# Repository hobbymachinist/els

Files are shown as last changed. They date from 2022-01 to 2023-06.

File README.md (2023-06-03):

# STM32 - Electronic Leadscrew

Electronic Leadscrew with STM32

## Demos

Some short demos available on YouTube

https://www.youtube.com/channel/UCVE05OvPm0yVd1yQSVZ0YSA/videos

## Building

```
git clone https://github.com/libopencm3/libopencm3
export OPENCM3_DIR=$PWD/libopencm3

cd libopencm3
make

cd ../
git clone <repo-url>
cd els

# edit Makefile to pick target and a TFT version
make TFT=ILI9481

# or
make TFT=ILI9486

# or
make TFT=ILI9488
```

Some ILITEK ICs use a non-standard 556 16-bit colorspace, use `COLORS=TFT_RGB_556` option in that case.

```
make TFT=ILI9488 COLORS=TFT_RGB_556
```

## Technical documentation

See [Technical Documentation](docs/els.md)

## Design ideas & Reference

- https://github.com/clough42/electronic-leadscrew
- https://github.com/prototypicall/Didge

## Goals / Features

1. The initial software is going to focus on being functional.
2. There is huge scope for optimisation, which can be something I might look into down the track.
3. Eventually, I'd like to add a G-code parser and motion controller to enable optional CNC control.

### Working with limited testing

* Z axis control for manual turning and threading operations
* Soft limits on Z & X
* Hard limits on Z & X
* Backlash compensation for leadscrews
* Semi automated cycles:
    - Turning
    - Threading
    - External Tapers
    - Internal Tapers
    - External Arcs
* Optional DRO support for:
    - TTL optical scales

### Wishlist / TO DO

* Semi automated cycles:
    - Internal Arc
    - External groove
    - Internal groove
* Tool radius compensation

## Pull Requests

Please reach out to discuss any major rewrites or changes if you wish to merge the changes upstream.

A lot of the firmware was developed over a few years on and off when I could find time to code and think about how I'd use it.
I don't want to disappoint or stop anyone from improving the software or hardware design but the primary focus of this work is
for my own personal use and don't want anything to distract me from that in a significant fashion. I don't have plenty of spare
time to review design changes or major software changes.

## IMPORTANT - PLEASE READ

Lathes are not toys, you can get injured or hurt someone else if you're not careful. Use this software at your
own risk.

This software is not provided with any warranty or support. It has only had limited testing in a home / hobby use setting
and may result in you getting injured or your equipment getting damaged due to errors in programming.

The author does not take any responsibility for the use of this software by others and cannot be held liable for any damages
that may result from its use.

## LICENSE

https://opensource.org/licenses/GPL-3.0

Free to be used in any fashion without royalty but any changes to hardware or software should be attributed and publicly shared
for the benefit of others.

Some of the code in this project uses snippets of code from [Adafruit GFX](https://github.com/adafruit/Adafruit-GFX-Library/)

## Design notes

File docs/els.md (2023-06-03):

# ELSv2

[TOC]

## Demos

Some short demos available on YouTube

https://www.youtube.com/channel/UCVE05OvPm0yVd1yQSVZ0YSA/videos

## Hardware

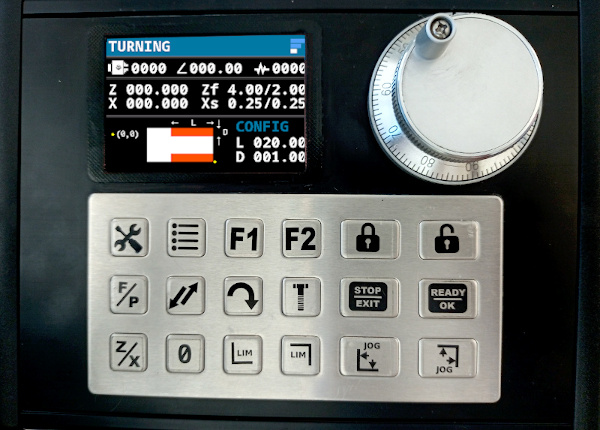
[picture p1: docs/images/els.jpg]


**IMPORTANT NOTE**

1. Ensure all signal cables are shielded.
2. Ensure the shielding is connected to ground at one end, close to the enclosure.
3. Ensure the enclosure is connected to power ground.
4. Always jog both axes to origin position (0, 0) before starting turning operations
    - This ensures any leadscrew backlash is taken care of in the lathe.
    - Allows the backlash compensation to kick in, ready for the turning steps.

### Kicad assets

All hw designs are done in Kicad 6.0.

- hw/els: The main board.
- hw/lcd: The LCD adapter for ILI9481 module

Optional extras:

- hw/buffer: Buffer and pulse shaper, helps keep the PUL signals going to the stepper drivers clean.
- hw/demo-driver: A standalone demo board with drv8825 for testing
- hw/power-clamp: Voltage clamp / suppression board.

### Main Board

Kicad files in hw/els

#### Active components

* Nucleo-F446RE https://www.st.com/en/evaluation-tools/nucleo-f446re.html
* GL850G USB HUB Controller
* CH340C USB UART
* FT24C64A EEPROM

#### Solder Bridge Changes and Modifications Needed to Nucleo64 446RE

The Nucleo 64 is connected to the main board USB hub with a small cable. Nucleo 446RE will need a fair few
jumper changes and soldering to permit the firmware to use the required GPIO pins.

Refer to the GPIO pins listed below in the GPIO Map, the solder bridges for these pins should be setup correctly. See Nucleo 446RE
documentation UM1724, Section 6.9 on Solder Bridges for more details. A quick summary for jumper settings and changes I've made.

| Jumper / Pad | State | Function |
|---|---|---|
| SB13 | REMOVE | PA2 for LCD |
| SB14 | REMOVE | PA3 for LCD |
| SB16 | REMOVE | HSE |
| SB21 | REMOVE | PA5 for LCD |
| SB50 | REMOVE | HSE |
| SB54 | REMOVE | HSE |
| SB55 | REMOVE | HSE |
| SB62 | ADD | Connects PA2 to D1 on CN9 |
| SB63 | ADD | Connects PA3 to D0 on CN9 |
| R35 | ADD | HSE, 0R or solder bridge |
| R37 | ADD | HSE, 0R or solder bridge |
| C33 | ADD | HSE, 18-22pF X7R Capacitor  |
| C34 | ADD | HSE, 18-22pF X7R Capacitor  |
| X3 | ADD | HSE, 8MHz HSE Crystal |
| D2 (CN9) | WIRE | Wire To CN3 TX for USART2 |
| D8 (CN5) | WIRE | Wire to CN3 RX for USART2 |

#### Using main board without USB hub & USB UART

The main board is primarily a breakout board for the Nucleo F446RE with a USB hub, USB USART controller
and additional terminal connectors. You can skip these (GL850G, CH340C and associated passives) and directly
wire PA9 and PA10 to the CN3 connectors marked RX and TX respectively. This will allow you to read the serial
comms via the onboard stlink CDC device.

The default UART baud rate in firmware is 921600, with 8 bits, no partity & 1 stop bit.

#### External Oscillator (HSE) on Nucleo 64

By default the firmware configures the clock to use the HSE. Nucleo 64 boards do not come with the crystal and passives
populated. Refer to UM1724 Section 6.7.1 for instructions on using HSE.

The following configuration is needed:
  - SB54 and SB55 OFF
  - R35 and R37 soldered
  - C33 and C34 soldered with 20 pF capacitors
  - SB16 and SB50 OFF

It's recommended to use an external crystal for better timing accuracy, but this is optional. If you want to use the
internal oscillator, set the `ELS_USE_HSE` directive to 0 in src/clock.c

#### EEPROM

This is again optional but without an external FT24C64A EEPROM, you will not be able to save the settings and the
defaults from constants.h will be used.

### TFT Breakout

Supported TFT 480x320 Displays

* ILI9481
* ILI9486
* ILI9488

AliExpress Links

* ILI9481 TFT LCD, https://www.aliexpress.com/item/1005001288341298.html
* ILI9486, ILI9488 TFT, https://www.aliexpress.com/item/1005001288341298.html

Kicad files in hw/lcd

This primarily a carrier / breakout board with an IDC ribbon cable connector to main board. The main board is
connected to the LCD module using an adapter board that breaks out the pins to a 16 pin IDC socket.

### Output buffer / pulse shaper

Kicad files in hw/buffer

Optional add-on for cleaning up the high frequency pulses from the main board to the stepper drivers. This needs to be powered
separately and co-located with the stepper drivers. You may not need this depending on the length of the signal cables from
the main board to the stepper drivers.

* CD4050BE, non-inverting hex buffer.
* CRE1S0505SC, isolated dc-dc converter 5v.

### Keypad

I used this because I had an unused one left over from a different project that did not work out. They're not cheap but they're
very reliable and resistant to liquids in the workshop. The seller can also laser etch the art for keypads if you're interested.

- IP65 18 Key, PS2 Keypad, https://www.aliexpress.com/item/1005002340320709.html

#### Input without keypad

You can make do with this for trying out the firmware by using UART as an input. To do it, edit src/usart.c and set
`ELS_USART_ENABLE_KEYPAD_INPUT` to 1

### Encoder

**IMPORTANT NOTE**

The spindle encoder PPR, along with the gear ratio and pulses per MM for Z axis determines the maximum spindle RPM and
thread pitch you can turn in threading operations. There is currently no warning displayed if the spindle PPR is less
than the minimum required PPR.

* Spindle Encoder: Optical 600PPR, https://www.aliexpress.com/item/4000392086291.html
* Hand wheel Encoder / pulser 100PPR 5v 4pin, https://www.aliexpress.com/item/32949618549.html

### Stepper motor & controller

* Z Stepper: 24HS40-5004D-E1000
  - https://www.omc-stepperonline.com/nema-24-closed-loop-stepper-motor-4-0-nm-566-56oz-in-encoder-1000cpr.html

* Z Controller: CL57Y
  - https://www.omc-stepperonline.com/y-series-closed-loop-stepper-driver-0-7-0a-24-50vdc-for-nema-17-23-24-stepper-motor.html

* X Stepper: NEMA23 1.2Nm 3A
  - https://www.aliexpress.com/item/1005002871654388.html

* X Controller: DM556
  - https://www.aliexpress.com/item/1005002628784693.html

### DRO

Supports TTL optical DROs and defaults to the commonly available 5uM resolution versions.

Most TTL optical DROs you get from China operate on a 5V logic level. You need to to get a DB9 panel or PCB socket (male)
and break out the 4 wires based on the wiring diagram for your DRO scale.

- +5V
- Ground
- Signal A
- Signal B

## Wiring / GPIO Map

```
PA0  - TFT Data
PA1  - TFT Data
PA2  - TFT Data
PA3  - TFT Data
PA4  - TFT Data
PA5  - TFT Data
PA6  - TFT Data
PA7  - TFT Data
PA8  - UNUSED
PA9  - USART TX
PA10 - USART RX
PA11 - DRO X-A (INTERRUPT)
PA12 - DRO X-B (INTERRUPT)
PA13 - UNUSED
PA14 - UNUSED
PA15 - UNUSED

PB0  - TFT RD
PB1  - DRO Z-A (INTERRUPT)
PB2  - UNUSED
PB3  - Spindle Enc A (INTERRUPT)
PB4  - Spindle Enc B
PB5  - DRO Z-B (INTERRUPT)
PB6  - TFT WR
PB7  - TFT RS
PB8  - TFT CS
PB9  - TFT RST
PB10 - EEPROM SCL
PB11 - N/A
PB12 - UNUSED
PB13 - Z ENA
PB14 - Z DIR
PB15 - Z PUL

PC0  - UNUSED
PC1  - UNUSED
PC2  - Input Enc A (INTERRUPT)
PC3  - Input Enc B
PC4  - PS/2 Keypad CLK (INTERRUPT)
PC5  - PS/2 Keypad DAT
PC6  - Spindle Enc A (Timer in Encoder mode)
PC7  - Spindle Enc B (Timer in Encoder mode)
PC8  - UNUSED
PC9  - UNUSED
PC10 - UNUSED
PC11 - UNUSED
PC12 - EEPROM SDA
PC13 - X ENA
PC14 - X DIR
PC15 - X PUL

PH0  - UNUSED
PH1  - UNUSED
```

## Keypad Layout

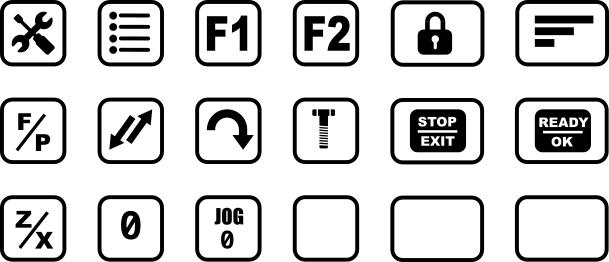
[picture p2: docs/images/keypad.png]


Keymap, left to right.

### Row 1

1. Settings
2. Lathe Functions
3. Special Function Key - F1
4. Special Function Key - F2
5. Keypad Lock / Unlock
6. Encoder multiplier change. Cyles through 1, 10 & 100.

### Row 2

1. Feed / Pitch
2. Reverse feed direction (not available in all functions)
3. Turning
4. Threading External
5. Stop Operation / Exit setting
6. Ready to start / Accept setting

### Row 3
1. Z/X axis setting
2. Zero Z / X axis
3. Jog to origin (depending on choice of Z or X axis setup)
4. Unused
5. Unused
6. Unused

## Lathe Functions

The manual turning and threading functions do not control the X axis / cross slide but allows turning
and threading operations at a given feed / pitch to a given length.

The remaining functions are stepper / servo driven on both Z (longitudinal along bed) and X (cross slide) axis.

All function screens display the spindle status at the top

1. Clockwise / Counter clockwise direction of spindle and RPM. Chuck icon is shown when RPM = 0
2. Angular position of the spindle in degrees. This can be used for any indexing functions.
3. Pulse counter, this is a function of the encoder PPR and wraps around. Threading operations synchronise to this value.

**NOTE**
1. Some lathe functions display diagrams where the stock to be removed is displayed in orange.
2. The origin (0,0) required for turning operations is displayed using a yellow dot.

### Settings

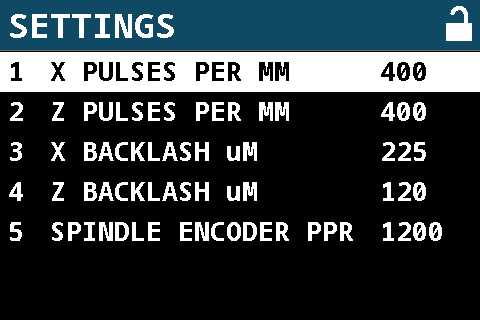
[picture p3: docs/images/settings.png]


#### X pulses per MM

X axis stepper / servo pulses per MM. This should include any gear ratios in transmission.

#### Z pulses per MM

Z axis stepper / servo pulses per MM. This should include any gear ratios in tranmission, especially if you're using
the gearbox.

#### X backlash uM

X backlash in microns. You can measure this by using a dial gauge against the cross slide and driving the stepper in
one direction for a full rotation and reversing to measure the amount of distance the stepper has to drive the axis before the
dial gauge indicates movement.

#### Z backlash uM

Z backlash in microns. Measure as above.

#### Spindle encoder PPR

Pulses per one revolution of the spindle. Note, this is usually the actual pulses generated by the encoder times any
gear ratios in drive mechanism. You can drive the encoder at 1.5-2x the speed of the spindle but pay attention to the
maximum RPM rating for the encoder.

#### X retract jog speed mm/s

Speed at which X axis retraction is done, can be slowed or sped up depending on gear / pulley ratios.

#### Z retract jog speed mm/s

Speed at which Z axis retraction is done, can be slowed or sped up depending on gear / pulley ratios.

#### X closed loop

If DRO is connected, then uses a simple closed loop traversal for linear movements on X axis. This can be particularly useful for turning stock to a specific diameter but it will depend on the accuracy of your DRO.

#### Z closed loop

If DRO is connected, then uses a simple closed loop traversal for linear movements on Z axis.

#### X DRO Invert

Invert direction for DRO on X Axis

#### Z DRO Invert

Invert direction for DRO on Z Axis

#### X DIR Invert

Invert stepper direction on X Axis

#### Z DIR Invert

Invert stepper direction on Z Axis

### Manual Turning

**NOTE**

When soft limits are turned on, with conventional turning the tool is moved from right to left along the Z axis at the
set feed rate until the minimum position is reached.

Steps:

1. Move tool to Z/X origin as required
2. Zero out Z and X axis optionally for DRO.
3. Set feed
4. Set length and enable soft limit (optional)
5. Turn on spindle
6. Press Ready to start
7. If soft limit is enabled, when the tool reaches the soft limit the feed will stop.
8. Back off tool, jog to Z origin.
9. Feed in tool and press Ready again

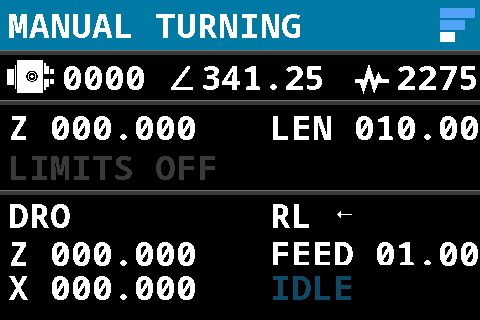
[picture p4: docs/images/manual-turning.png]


#### F/P

Set feed. The feed rate is independent of the spindle RPM at mm/s.

#### Reverse direction

Reverses feed direction. The usual direction is right to left towards spindle.

#### Z/X

1. Set Z axis, jogging
2. Pressing the button again switches to X axis setting, only used for zeroing the DRO reading (if available).

#### 0

Zero Z axis or X axis (DRO)

#### F1

Set the length to turn, Z soft limit target.

#### F2

Turns on / off soft limits. This will stop Z drive when the position reaches Z min.

#### Jog to Z origin

Jog Z axis to origin position

### Manual Threading

**NOTE**

When soft limits are turned on, with conventional turning the tool is moved from right to left along the Z axis at the
set pitch ratio until the minimum position is reached.

Steps:

1. Move tool to Z/X origin as required
2. Zero out Z and X axis
3. Set pitch
4. Set length
5. Turn on spindle
6. Press Ready to start
7. When the tool reaches the soft limit, it will stop.
8. Back off tool, press Jog to origin
9. Feed in tool and press Ready again

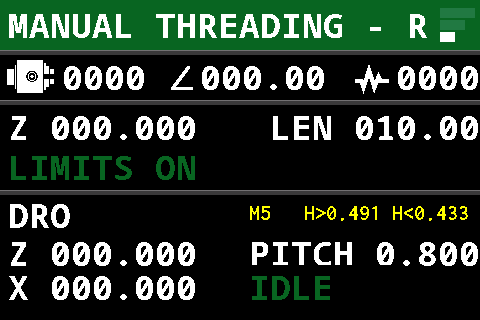
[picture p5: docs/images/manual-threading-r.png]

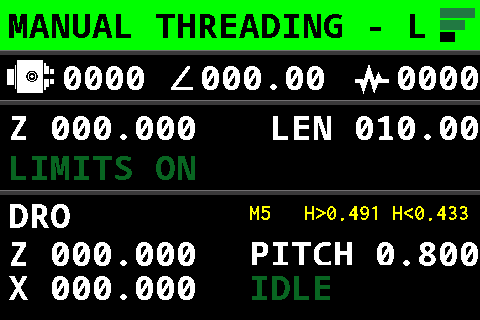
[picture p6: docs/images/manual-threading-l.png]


#### F/P

Choose pitch - the pitch determines the feed rate and this is tied to the rotation of the spindle.

You can pick a standard metric pitch with the displayed thread crest dimension. Pressing the key again will allow you to set
an arbitrary pitch value. This can be used to turn approximate imperial threads.

#### Reverse direction

While in pitch settings, pressing reverse feed direction allows you cut left hand threads or right hand threads.

#### Z/X

1. Set Z axis, jogging and setting min / max positions for virtual stop.
2. Pressing the button again switches to X axis setting, only used for zeroing the DRO reading.

#### 0

Zero Z axis or X axis (DRO)

#### F1

Set length

#### F2

Unused

#### Jog Z to Origin

Jog Z axis to 0 position

### Turning

Steps:

1. Move tool to Z/X origin as required
2. Zero out Z and X axis
3. Set roughing feed and feed for finish pass
4. Set the roughing depth of cut and depth of cut for finish pass
4. Set length and turning depth
5. Turn on spindle
6. Press Ready to start

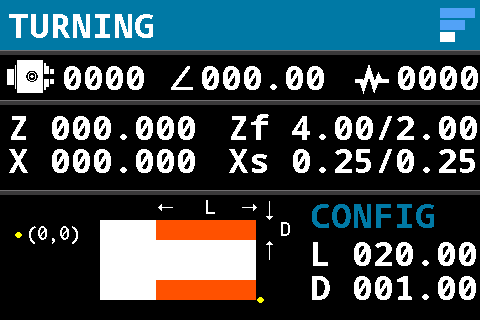
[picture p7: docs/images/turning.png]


#### F/P

Set feed & depth of cut.

NOTE: The feed rate is independent of the spindle RPM at mm/s.

Press key to cycle through

1. roughing feed rate in mm/s
2. finishing pass feed rate in mm/s
3. roughing depth of cut in mm
4. finishing pass feed rate in mm/s

#### Z/X

1. Z axis jogging.
2. Press key again for X axis jogging

#### 0

Zero Z axis or X axis (DRO)

#### F1

1. Set length
2. Press key again to set depth

#### F2

Display DRO or diagram.

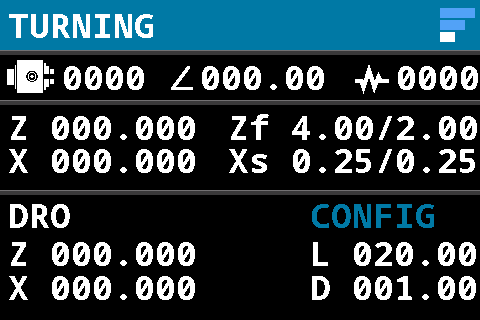
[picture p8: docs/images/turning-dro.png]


### Facing

Steps:

1. Move tool to Z/X origin as required
2. Zero out Z and X axis
3. Set feed
4. Set depth of cut on Z for each pass
4. Set length on Z axis to face and depth (radius of stock to face)
5. Turn on spindle
6. Press Ready to start

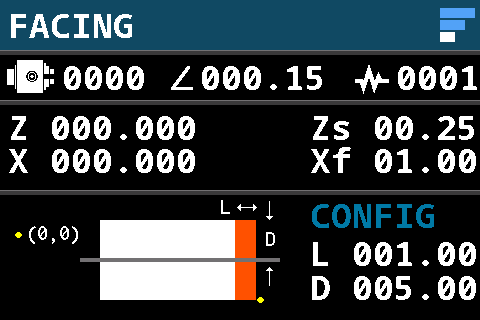
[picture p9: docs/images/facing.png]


#### F/P

Set feed (Xf) & depth of cut (Zs).

#### Z/X

1. Z axis jogging.
2. Press key again for X axis jogging

#### 0

Zero Z axis or X axis (DRO)

#### F1

1. Set length
2. Press key again to set depth

#### F2

Display DRO or diagram.

### Parting

Steps:

1. Move tool to Z/X origin as required
2. Zero out Z and X axis
3. Set feed (Xf)
4. Set depth of cut (radius of stock to part off)
5. Set retraction rate (Rx) if needed. e.g. if set to 2mm, this retracts the tool 5mm for every 2mm of in-feed.
5. Turn on spindle
6. Press Ready to start

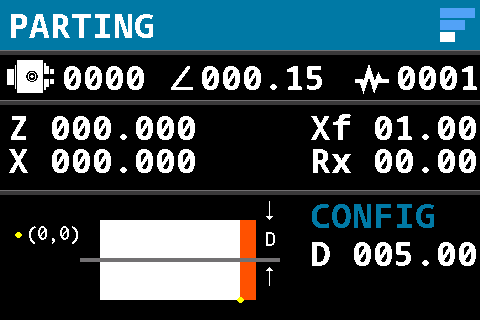
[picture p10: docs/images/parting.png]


#### F/P

Set feed (Xf) & retraction (Rx).

#### Z/X

1. Z axis jogging.
2. Press key again for X axis jogging

#### 0

Zero Z axis or X axis (DRO)

#### F1

Set total depth to part off, this is half the stock diameter ideally.

#### F2

Display DRO or diagram.

### Boring Pocket

Steps:

1. Move tool to Z/X origin as required
2. Zero out Z and X axis
3. Set feed and depth of cut
4. Set depth and turning radius
5. Turn on spindle
6. Press Ready to start

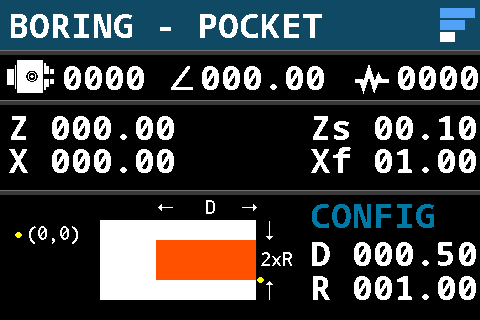
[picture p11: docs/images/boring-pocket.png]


#### F/P

1. Set feed. The feed rate is independent of the spindle RPM at mm/s.
2. Press key again to set depth of cut for turning pass.

#### Z/X

1. Z axis jogging.
2. Press key again for X axis jogging

#### 0

Zero Z axis or X axis (DRO)

#### F1

1. Set depth
2. Press key again to set radius

The diameter of the bore is twice the radius.

#### F2

Display DRO or diagram.

### Boring Hole

Steps:

1. Move tool to Z/X origin as required
2. Zero out Z and X axis
3. Set feed and depth of cut
4. Set depth and width for stock removal
5. Turn on spindle
6. Press Ready to start

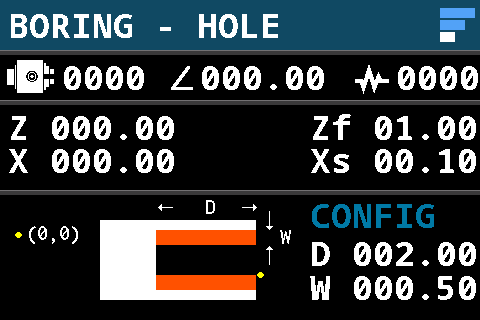
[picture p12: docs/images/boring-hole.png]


Use this if you have drilled a hole or performing boring operation with a through hole.

#### F/P

1. Set feed. The feed rate is independent of the spindle RPM at mm/s.
2. Press key again to set depth of cut for turning pass.

#### Z/X

1. Z axis jogging.
2. Press key again for X axis jogging

#### 0

Zero Z axis or X axis (DRO)

#### F1

1. Set depth
2. Press key again to set width of stock to remove.

#### F2

Display DRO or diagram.

### Knurling

Uses a form of bidirectional multi-start threading operation to cut knurls. Given the large pitch sizes required,
it's best to hand turn the spindle or use RPM < 30.

Steps:

1. Move tool to Z/X origin as required
2. Zero out Z and X axis
3. Set (L) length of the stock to knurl
4. Set (d) depth to cut
5. Set (D) diameter of stock
6. Set (A) lead angle, default to 30 deg.
7. Set (N) number of knurls.
8. Turn on spindle
9. Press Ready to start

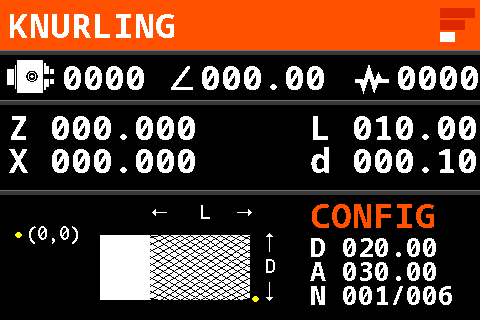
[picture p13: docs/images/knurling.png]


#### Z/X

1. Z axis jogging.
2. Press key again for X axis jogging

#### 0

Zero Z axis or X axis (DRO)

#### F1

Sets length, cut depth, diameter, lead angle and knurl count. Press F1 again to cycle through the settings.

#### F2

Display DRO or diagram.

### External Threading

Steps:

1. Move tool to Z/X origin as required
2. Zero out Z and X axis
3. Set pitch (and optionally thread height)
4. Set length and depth of cut
5. Turn on spindle
6. Press Ready to start

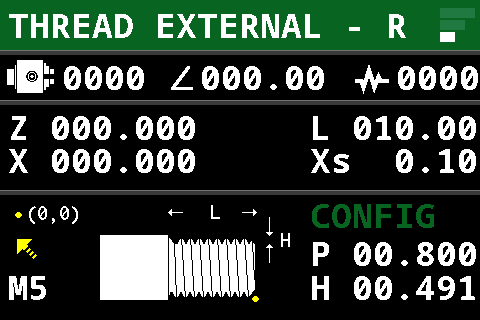
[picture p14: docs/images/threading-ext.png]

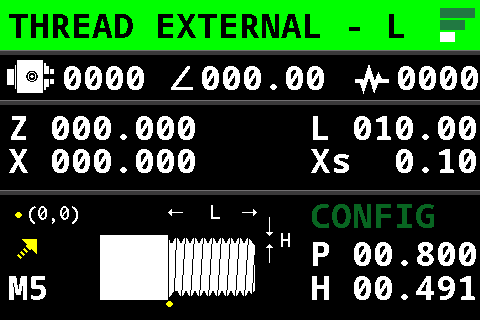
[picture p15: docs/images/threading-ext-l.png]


#### F/P

1. Select pitch, cycles through standard metric pitches.
2. Press key again to set an arbitrary pitch and thread height / depth.
3. Press "Reverse Direction (`</>`)" button to switch between RH and LH threads.

#### Z/X

1. Z axis jogging.
2. Press key again for X axis jogging

#### 0

Zero Z axis or X axis (DRO)

#### F1

IMPORTANT: The diagonal infeed hard codes the angle to 26.565° which is only valid for 60° thread profiles.

1. Set length of thread
2. Press key again to set depth of cut.
3. While in depth of cut selection press "Reverse Direction (`</>`)" button to switch between plunge and diagonal in-feed.

#### F2

Display DRO or diagram.

### Internal Threading

TODO: add support for LH threads and diagonal in-feed

Steps:

1. Move tool to Z/X origin as required
2. Zero out Z and X axis
3. Set pitch (and optionally thread depth)
4. Set length and depth of cut
5. Turn on spindle
6. Press Ready to start

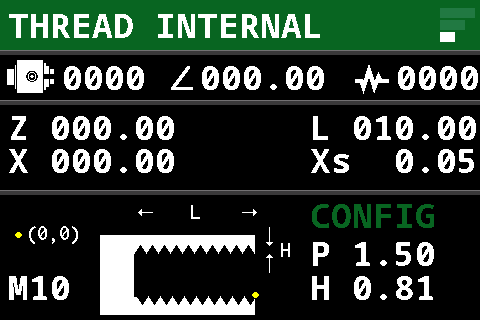
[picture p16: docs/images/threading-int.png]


#### F/P

1. Select pitch, cycles through standard metric pitches.
2. Press key again to set an arbitrary pitch and thread height / depth.

#### Z/X

1. Z axis jogging.
2. Press key again for X axis jogging

#### 0

Zero Z axis or X axis (DRO)

#### F1

1. Set length of thread
2. Press key again to set depth of cut.

#### F2

Display DRO or diagram.

### External Taper - Right

Steps:

1. Move tool to Z/X origin as required
2. Zero out Z and X axis
3. Set feed and depth of cut
4. Set length and depth of taper. Press F2 - The angle should be displayed in addition to DRO values.
5. Turn on spindle
6. Press Ready to start

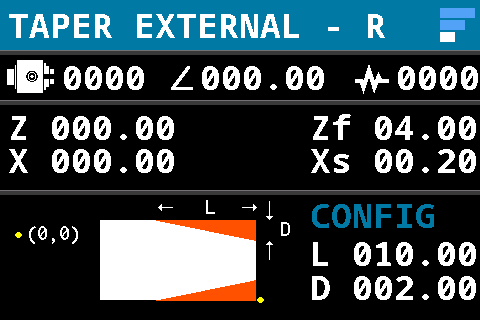
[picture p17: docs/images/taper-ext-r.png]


#### F/P

1. Select feed, mm/s.
2. Press key again to set depth of cut.

#### Z/X

1. Z axis jogging.
2. Press key again for X axis jogging

#### 0

Zero Z axis or X axis (DRO)

#### F1

1. Set length of taper
2. Press key again to set depth of taper.

#### F2

Display DRO or diagram. This also displays the taper angle.

### External Taper - Left

Steps:

1. Move tool to Z/X origin as required
2. Zero out Z and X axis
3. Set feed and depth of cut
4. Set length and depth of taper. Press F2 - The angle should be displayed in addition to DRO values.
5. Turn on spindle
6. Press Ready to start

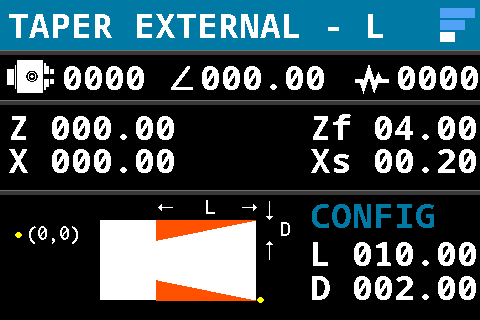
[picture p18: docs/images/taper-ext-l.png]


#### F/P

1. Select feed, mm/s.
2. Press key again to set depth of cut.

#### Z/X

1. Z axis jogging.
2. Press key again for X axis jogging

#### 0

Zero Z axis or X axis (DRO)

#### F1

1. Set length of taper
2. Press key again to set depth of taper.

#### F2

Display DRO or diagram. This also displays the taper angle.

### Internal Taper

Steps:

1. Move tool to Z/X origin as required
2. Zero out Z and X axis
3. Set feed and depth of cut
4. Set length and depth of taper. Press F2 - The angle should be displayed in addition to DRO values.
5. Turn on spindle
6. Press Ready to start

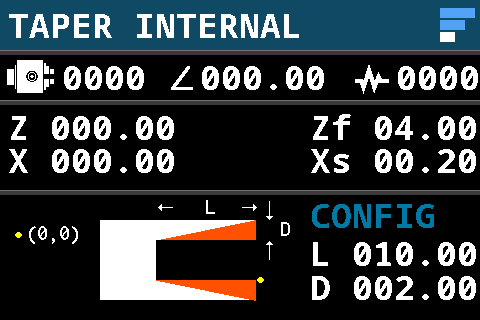
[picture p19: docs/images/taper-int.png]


#### F/P

1. Select feed, mm/s.
2. Press key again to set depth of cut.

#### Z/X

1. Z axis jogging.
2. Press key again for X axis jogging

#### 0

Zero Z axis or X axis (DRO)

#### F1

1. Set length of taper
2. Press key again to set depth of taper.

#### F2

Display DRO or diagram. This also displays the taper angle.

### Convex External - Right

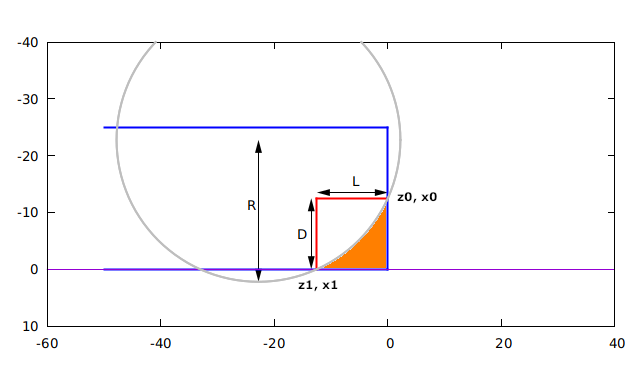
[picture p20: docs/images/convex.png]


Glossary:

1. (z0, x0) and (z1, x1), intersection of arc with stock.
2. Radius: Radius of the arc.
3. Depth: depth of arc, x1 - x0
4. Length: length of arc, z1 - z0

Varying the radius, length and depth will allow a variety of convex curves to be turned.

Steps:

1. Move tool to Z/X origin as required
2. Zero out Z and X axis
3. Set feed and depth of cut
4. Set radius, length and depth of arc.
5. Turn on spindle
6. Press Ready to start

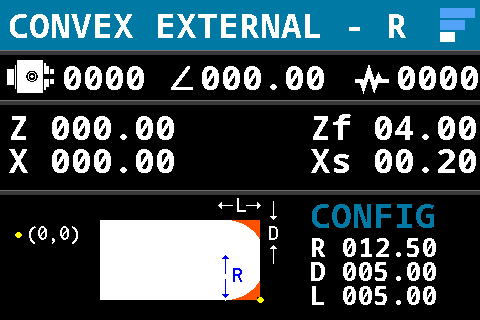
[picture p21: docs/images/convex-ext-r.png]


#### F/P

1. Select feed, mm/s.
2. Press key again to set depth of cut.

#### Z/X

1. Z axis jogging.
2. Press key again for X axis jogging

#### 0

Zero Z axis or X axis (DRO)

#### F1

1. Set radius of circle
2. Press key again to set depth.
3. Press key again to set length.

#### F2

Display DRO or diagram.

### Convex External - Left

Steps:

1. Move tool to Z/X origin as required
2. Zero out Z and X axis
3. Set feed and depth of cut
4. Set radius, length and depth of arc.
5. Turn on spindle
6. Press Ready to start

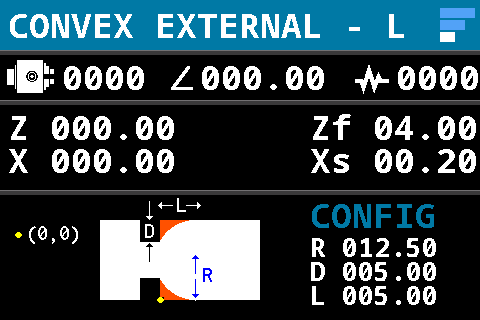
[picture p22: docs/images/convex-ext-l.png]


#### F/P

1. Select feed, mm/s.
2. Press key again to set depth of cut.

#### Z/X

1. Z axis jogging.
2. Press key again for X axis jogging

#### 0

Zero Z axis or X axis (DRO)

#### F1

1. Set radius of circle
2. Press key again to set depth.
3. Press key again to set length.

#### F2

Display DRO or diagram.

### Concave External - Right

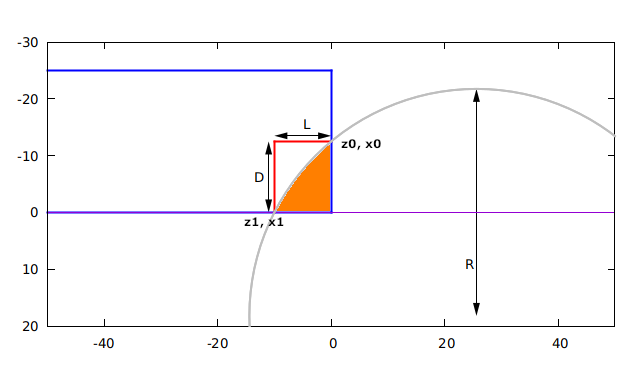
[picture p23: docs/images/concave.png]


Glossary:

1. (z0, x0) and (z1, x1), intersection of arc with stock.
2. Radius: Radius of the arc.
3. Depth: depth of arc, x1 - x0
4. Length: length of arc, z1 - z0

Steps:

1. Move tool to Z/X origin as required
2. Zero out Z and X axis
3. Set feed and depth of cut
4. Set radius, length and depth of arc.
5. Turn on spindle
6. Press Ready to start

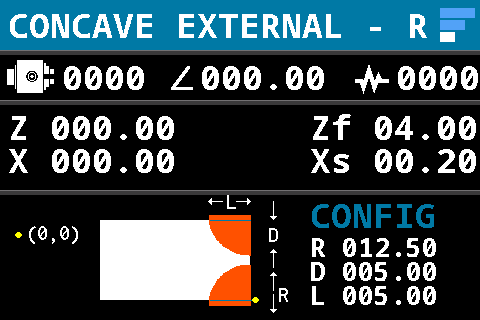
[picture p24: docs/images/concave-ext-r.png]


#### F/P

1. Select feed, mm/s.
2. Press key again to set depth of cut.

#### Z/X

1. Z axis jogging.
2. Press key again for X axis jogging

#### 0

Zero Z axis or X axis (DRO)

#### F1

1. Set radius of circle
2. Press key again to set depth.
3. Press key again to set length.

#### F2

Display DRO or diagram.

### Concave External - Left

TODO

### Rounded Groove

TODO

### Straight Groove

TODO

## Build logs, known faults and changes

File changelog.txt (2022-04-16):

2022-04-16

* increase stepper position resolution display
* add a new function for diamond cut knurling

2022-04-09

* replaced encoder acceleration with manual multiplier selection (1, 10, 100)
* added support for closed loop linear moves on Z & X axes
* updated convex turning to specify arbitrary convex arcs
* implementation for right handed concave arc
* reduced spindle encoder resolution for threading, improves responsiveness

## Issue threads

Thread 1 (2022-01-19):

G-code parser

ebo, 2022-01-19:
Decades ago I wrote a g-code parser using Spirit+ (part of the Boost libraries).  It came complete with runtime overloading of commands (so you could run different flavors of RD274*).  That project was WAY overkill and probably would not fit into what you have in mind, but I could probably salvage chunks to be useful.  So, tell me what you want the parser to do, and maybe PM me, and we can discuss seeing if any of it would be useful.

hobbymachinist, 2022-01-19:
Thanks @ebo, the rough plan is to get a modified version of Grbl integrated as a module to allow CNC control of X and Z axis along with spindle sync. If that works, I can get rid of the bespoke stepper controller in els and rewrite almost all the stock turning operations as canned cycles that can be fed into Grbl.

qtron, 2022-06-02:
Hi HM,
help! i'm stuck.. not familiar w github at all, lost a LOT of time trying to find the documentation, circuit diagram & gerber files etc.. i saw a gpio list but not sure what that all means!
i have built a Russian 2 axis arduino Mega ELS & seems to work, but i much prefer yours with the magic, albeit expensive!! keypad.
- I also can't find info on how U re labelled it, so nicely!!
- Do U have a list of the specs of the ELS (i dont mean characteristics)?
- Can U move the els in 0.01mm increments?
- What is the max allowable backlash your s/w can cope with?
- i saw the vid of the failed reverse taper.. what was wrong? some words would help!

Without a circuit diagram i have no way of knowing how to set it up, & install/ program the Eprom i saw mentioned.. where did U get it from? How did U program it?

I see its been a while since u were here last, so hope ur ok.

I did download the zip file for the code but cant see how to download the documentation.
i have no idea what a fork is, pull requests, etc.. does pull mean remove ur files?!!
Sorry but i find github strange indeed.
eg, Why does one need to see the inner workings of a gerber file here?
i have kicad & use JLCPCB quite a bit , could see gerber files but they are all individual - how do U download all at once? surely they are zipped?
Thanks!
Qtron

hobbymachinist, 2022-06-03:
The schematics are split into multiple modules, you can open them up in Kicad to have a look.

Main board: https://github.com/hobbymachinist/els/blob/main/hw/els/els.sch  or https://github.com/hobbymachinist/els/blob/main/hw/els/els.pdf
LCD breakout https://github.com/hobbymachinist/els/blob/main/hw/lcd/lcd.sch

> i saw a gpio list but not sure what that all means!

Here's a very brief summary how the pins are mapped,
https://github.com/hobbymachinist/els/blob/main/src/gpio.h#L25-L81

You are expected to have some knowledge of electronics, microcontrollers and writing firmware. This project is not designed to be consumer ready if you're not able to understand how all of these go together unfortunately.

> Do U have a list of the specs of the ELS

What do you mean by specs ?

> Can U move the els in 0.01mm increments?

This depends on your servo / stepper driver settings (usually called micro steps), the smallest increment I can move my axes is 0.0025mm

> What is the max allowable backlash your s/w can cope with?

Any arbitrary amount, but this needs to be constant and cannot vary by direction. I have since stopped relying on this as the backlash can drift over time leading to inaccurate movements.

I would recommend switching over to ball screw if you want 2 axes precision control or use an optical DRO scale and connect that to the ELS. The ELS now supports limited closed loop movement on both axis by using the DRO for feedback and compensates for backlash accordingly.

> i saw the vid of the failed reverse taper.. what was wrong? some words would help!

It was a control loop bug and was not setting the stepper direction pulse correctly, I've fixed it.

> does ur ELS do the calcs on the fly, like Clough42's ELS?

yes, the micro controller used is very capable. STM32F446RE can handle a lot more if the internal features are use correctly. I'm not taking advantage of all the features yet and it seems to work fine for me.

> Why does one need to see the inner workings of a gerber file here?
> i have kicad & use JLCPCB quite a bit , could see gerber files but they are all individual - how do U download all at once?

If you have Kicad, you can open the project files under the hw directory and have a look, export the gerbers as needed for your purpose but as I said, this project is not going to be ready to use out of the box unless you have some basic knowledge of microcontrollers, electronics and firmware programming.

hobbymachinist, 2022-06-03:
@qtron if you're not comfortable with a full DIY solution, I would recommend you take a look at Rocketronics ELS https://www.rocketronics.de/en/els/. It is ready to use and comes with excellent documentation.

qtron, 2022-06-03:
hiya HM,
i am comfortable! as i said i built the russian 2 axis els..(ver 7e2)
its not so easy to use.

i just need the info. of your nice creation to proceed, if possible.
Yours is the only one with knurling,
  (as well as ricketronics does have issues.
a guy on youtube evaluated it, and some glitches can be seen, like not starting threading! its expensive too ).

pls advise:
does yours do calcs on the fly?

how do i find the cct diagram to load into kicad?
As i said, navigating thru Github trying to find downloads is hard! (obviously not for some!)
PLEASE advise..
thankyou😃

On 3 June 2022 12:34:48 GMT+10:00, hobbymachinist ***@***.***> wrote:
***@***.*** if you're not comfortable with a full DIY solution, I would recommend you take a look at Rocketronics ELS https://www.rocketronics.de/en/els/. It is ready to use and comes with excellent documentation.
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
..
Sent from mob. Ph.

qtron, 2022-06-03:
sorry HM, i just found your previous email! much appreciated
the rocketronics unit basic ver 4, delivered is $422 AUD.

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
***@***.*** if you're not comfortable with a full DIY solution, I would recommend you take a look at Rocketronics ELS https://www.rocketronics.de/en/els/. It is ready to use and comes with excellent documentation.
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
..
Sent from mob. Ph.

qtron, 2022-06-03:
i am most grateful for the links to the files, but is there a place in github where i can download them, to get into kicad?

by move 0.01mm , i meant move from the control panel, not microstep movement..

Specs: like max settable X & Z motion,
respose time after go button pressed,
lag time of tool vs steps issued,
any step misses at high speed,

absolutely wonderful re closed loop.
i saw the glass scale on your Z motion, (but didnt know if it was just DRO).

BTW,
i saw in MEW that Joe Noci (of Nairobi) uses a rattle damper on his stepper to kill any resonance! it is supposed to help greatly , accel. from zero.

kind regards,

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
..
Sent from mob. Ph.

hobbymachinist, 2022-06-03:
Go to the repository page, https://github.com/hobbymachinist/els and download the zip file as shown

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

> by move 0.01mm , i meant move from the control panel, not microstep movement..

0.005mm

> Specs: like max settable X & Z motion,

There are no soft limits, only what you set the limits to in the program.

> respose time after go button pressed,

Probably 50-100ms. If you're thinking about threading it synchronises to the encoder counter so even if you press it will only start at the spindle position when encoder counter is at a certain value.

> lag time of tool vs steps issued,

speed of light :)   it's probably a few microseconds due to the stepper / servo drivers.

> any step misses at high speed,

not that I have noticed, I use closed loop hybrid steppers that will stall if they cannot keep up but there is no acceleration support for threading - so your mileage may vary depending on your hardware choice.

qtron, 2022-06-03:
thanks again😃
i had already downloaded the zipped MCU f/w.
i mean download the schematics, the wiring hookup diagram to the eprom, & the overall layout..

i saw the list from the links u sent earlier, clicked on ''copy path'', tried
''permlink copy'' etc. .. nothing happened.
just dunno how to get the sch into kicad,
and how to get the zipped gerber files.
cheers,

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
..
Sent from mob. Ph.

Closed 2022-06-03.

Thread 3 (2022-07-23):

Questions

kzali, 2022-07-23:
Hi
Firstly I'd like to thank you for such a well though project.  I am happy to say that I have gotten all the PCB's and the Neucleo board
The LCD, Encoder, Keyboard, and the hand wheel are on the way.  I intend to build it slowly as have beginner level skills (largely in simple Arduino projects.)

1.  I am having a hard time sourcing the FT24C64A EEPROM, CH340C USB UART and the GL850G USB HUB Controller, here in Australia.  I understand from your very detailed technical
    documentation that I can do without the CH340C and the GL850G (and their passive components)  I will however directly wire PA9 and PA10 to the CN3 connectors marked RXand TX on the Nucleo.

2.  There seem to be many i2c 8 pin 64k EEPROMS on au.rsonline and other suppliers! Any suggestions/alternate will be greatly appreciated.

3.  I am not clear what this means "Nucleo 446RE will need a fair few jumper changes and soldering to permit the firmware to use the required GPIO pins. Refer to the GPIO pins listed below, the solder bridges for these pins should be setup correctly. See Nucleo 446RE documentation UM1724, Section 6.9 on Solder Bridges."  I have tried to figure it out without any success from the UM1724 documentation.  I am assuming that the jumper changes are on the Neuclo but am confused about the 15 TerminalBlock_bornier-
2_P5.08mm and suspect that the bridges are related to this.  Your direction will be highly appreciated **(perhaps an image of the populated board.)

5.  After failing to setup the Toolchain on windows via cygwin, I succeeded in setting it up on a Raspberry Pi 400 and it compiled without any issues.  Was wondering if this can be accomplished with CubeMX!

6.  I intend to use the demo driver board to first test this with a toy lathe (Thefirsttool Tz20002mr) that I have had for a while, using Nema 17 motors.  And Eventually install on My Sieg C3.

I am located in the Sydney region and have extra PCB's will be happy to send you a couple of sets if you need it considering you are in Australia.  My email: kzaliaust@gmail.com.  Many thanks for your help

Regards
Kamran Zali

Closed 2022-07-23.

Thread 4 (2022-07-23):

Questions

kzali, 2022-07-23:
Hi
Firstly I'd like to thank you for such a well though project. I am happy to say that I have gotten all the PCB's and the Neucleo board
The LCD, Encoder, Keyboard, and the hand wheel are on the way. I intend to build it slowly as have beginner level skills (largely in simple Arduino projects.)

I am having a hard time sourcing the FT24C64A EEPROM, CH340C USB UART and the GL850G USB HUB Controller, here in Australia. I understand from your very detailed technical
documentation that I can do without the CH340C and the GL850G (and their passive components) I will however directly wire PA9 and PA10 to the CN3 connectors marked RXand TX on the Nucleo.

There seem to be many i2c 8 pin 64k EEPROMS on au.rsonline and other suppliers! Any suggestions/alternate will be greatly appreciated.

I am not clear what this means "Nucleo 446RE will need a fair few jumper changes and soldering to permit the firmware to use the required GPIO pins. Refer to the GPIO pins listed below, the solder bridges for these pins should be setup correctly. See Nucleo 446RE documentation UM1724, Section 6.9 on Solder Bridges." I have tried to figure it out without any success from the UM1724 documentation. I am assuming that the jumper changes are on the Neuclo but am confused about the 15 TerminalBlock_bornier-
2_P5.08mm and suspect that the bridges are related to this. Your direction will be highly appreciated **(perhaps an image of the populated board.)

After failing to setup the Toolchain on windows via cygwin, I succeeded in setting it up on a Raspberry Pi 400 and it compiled without any issues. Was wondering if this can be accomplished with CubeMX!

I intend to use the demo driver board to first test this with a toy lathe (Thefirsttool Tz20002mr) that I have had for a while, using Nema 17 motors. And Eventually install on My Sieg C3.

I am located in the Sydney region and have extra PCB's will be happy to send you a couple of sets if you need it considering you are in Australia. My email: [kzaliaust@gmail.com](mailto:kzaliaust@gmail.com). Many thanks for your help

Regards
Kamran Zali

hobbymachinist, 2022-07-23:
> I intend to build it slowly as have beginner level skills (largely in simple Arduino projects.)

Just ask questions on this issue, so it can function as a reference for others. Just setting the expectations and caveats perhaps too late sine you're committed now :)

- It's a personal project I work on in my spare time - so there's definitely a few rough edges.
- I would normally guide people towards Acorn, Masso, Mach4 or even LinuxCNC - I only started building this because I like using my lathe manually most of the time, ELS is something that helps with repetitive work / tapers etc.
- Backlash compensation is extremely tricky to get right, especially on Z with the way half nuts engage determining the backlash at times. So backlash can potentially vary over time in my observation, needs calibration every single time before you do something.
- I have installed an optical linear scale with 5uM resolution and use this for closed loop feedback instead of backlash compensation.

> I am having a hard time sourcing the FT24C64A EEPROM, CH340C USB UART and the GL850G USB HUB Controller, here in Australia.

I would skip the USART and USB HUB controller, it's only there because I was initially planning to use the HUB for a second daughter board in the future.

> I will however directly wire PA9 and PA10 to the CN3 connectors marked RXand TX on the Nucleo.

This will work fine, I use this for my second dev kit I use for testing.

> There seem to be many i2c 8 pin 64k EEPROMS on au.rsonline and other suppliers! Any suggestions/alternate will be greatly appreciated.

You should be able to use any 24C64A eeprom in the compatible SO-8 package. They all have the same pinouts and usually have the same read / write control loop / implementation.

>  I have tried to figure it out without any success from the UM1724 documentation. I am assuming that the jumper changes are on the Neuclo but am confused about the 15 TerminalBlock_bornier-2_P5.08mm and suspect that the bridges are related to this.

Can you elaborate ? for each of the GPIO listed in the UM1724 solder bridge section, you need to remove or add the jumper as explained in the user manual to allow the pin to be routed to the external GPIO (disconnected from the default Nucleo function).

Additionally you will also need to
- solder the bridges for the external high frequency (HSE) crystal.
- solder 2 capacitors, I think 18pF

> After failing to setup the Toolchain on windows via cygwin, I succeeded in setting it up on a Raspberry Pi 400 and it compiled without any issues. Was wondering if this can be accomplished with CubeMX!

I use libopencm3, so CubeMX will no help. If you're using Windows 10, you should have better luck with WSL and ARM GCC.

http://cs107e.github.io/guides/install/wsl/

> I intend to use the demo driver board to first test this with a toy lathe (Thefirsttool Tz20002mr) that I have had for a while, using Nema 17 motors. And Eventually install on My Sieg C3.

Yeah go for it, pay attention to polarity, DRV8825 is very picky, fries easy and needs a heat sink.

I have a fair few extra boards around, once the STM32 shortage eases I will most likely respin the board to ditch the Nucleo 64. The only reason I went with that is it was it was impossible to get STM32F446 on tape when I started building this :)

Good luck!

hobbymachinist, 2022-07-23:
and use shielded cables for everything, DC motors or VFD + AC 3ph motor, TFT etc everything is a noise generator, so shield everything :|

kzali, 2022-07-23:
Hi many thanks for a prompt response
> * Pay attention to cable shielding, if possible use ferrite ribbon cable for the TFT (TFTs are very noisy at high speed).
Noted had to do shielded cabling even for a Grbl controller

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

I had meant "There seem to be many i2c 8 pin 64k EEPROMS on au.rsonline and other suppliers!  But  NO 24C64A in SO-8 (seems to be a shortage of these)  So any suggestions?
>
> > I have tried to figure it out without any success from the UM1724 documentation. I am assuming that the jumper changes are on the Neuclo but am confused about the 15 TerminalBlock_bornier-2_P5.08mm and suspect that the bridges are related to this.
>
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
Thankyou

deepfryed, 2022-07-23:
> I had meant "There seem to be many i2c 8 pin 64k EEPROMS on au.rsonline and other suppliers! But NO 24C64A in SO-8 (seems to be a shortage of these) So any suggestions?

wow, even eeproms ?! geee

try LCSC https://lcsc.com/products/EEPROM_502.html?keyword=24C64A

> I am assuming that the jumper changes are on the Neuclo

Yes, all of the jumper changes are on the Nucleo 64 board. No need to to bodge anything on the ELS main board PCB, unless you need to customise something.

You will need to do some point to point wiring for DRO connection if you choose to add that.

hobbymachinist, 2022-07-23:
> I had meant "There seem to be many i2c 8 pin 64k EEPROMS on au.rsonline and other suppliers! But NO 24C64A in SO-8 (seems to be a shortage of these) So any suggestions?

wow, even eeproms ?! geee

try LCSC https://lcsc.com/products/EEPROM_502.html?keyword=24C64A

> I am assuming that the jumper changes are on the Neuclo

Yes, all of the jumper changes are on the Nucleo 64 board. No need to to bodge anything on the ELS main board PCB, unless you need to customise something.
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
hobbymachinist, 2022-08-01:
@kzali did you manage sourcing the EEPROM, this might be pin and protocol compatible but half the storage size which may be enough (you need to double check the datasheet) and is available from Rockby in Melbourne. The firmware code needs to be modified if you use this.

https://www.rockby.com.au/SearchresSql_12.cfm?Searchkey=AT24C32N

kzali, 2022-08-01:
> @kzali did you manage sourcing the EEPROM, this might be pin and protocol compatible but half the storage size which may be enough (you need to double check the datasheet) and is available from Rockby in Melbourne. The firmware code needs to be modified if you use this.
>
> https://www.rockby.com.au/SearchresSql_12.cfm?Searchkey=AT24C32N

@hobbymachinist Thanks for the heads up,  I will be visiting my country of origin and have a micro Shenzhen, in my home town and have sourced all the components there.  At better prices that Aliexpress as well!  In fact will be carrying one set of boards as its very cheap to have them populated by professional services.  Will probably bring some extra components, for future projects.  Have the keyboard with me and the encoder and the pulse wheel expected today.

Still was only able to setup the toolchain on the raspberry pi 400 while on WSL and a Ubuntu VM I get this error  (Don't know what I am doing wrong!
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
So googling away

hobbymachinist, 2022-08-01:
It might be easier to read if you copy paste the error text. The screenshot is hard to read on my phone.

I can see `-I/home/billa/els/libopencm3/include`  is there a libopencm3 directory there ?

> Will probably bring some extra components, for future projects.

excellent, see if you find a cut tape of stm32f446re at good price lol

kzali, 2022-08-01:
billa@billa:~/libopencm3$ cd ~
billa@billa:~$ cd els
billa@billa:~/els$ arm-none-eabi-gcc  --version
arm-none-eabi-gcc (15:9-2019-q4-0ubuntu1) 9.2.1 20191025 (release) [ARM/arm-9-branch revision 277599]
Copyright (C) 2019 Free Software Foundation, Inc.
This is free software; see the source for copying conditions.  There is NO
warranty; not even for MERCHANTABILITY or FITNESS FOR A PARTICULAR PURPOSE.

billa@billa:~/els$ make
rules.mk:60: Cannot find libopencm3 library in the standard search paths.
rules.mk:61: *** Please specify it through OPENCM3_DIR variable!.  Stop.
billa@billa:~/els$ export OPENCM3_DIR=$PWD/libopencm3
billa@billa:~/els$ make
Using /home/billa/els/libopencm3 path to library
arm-none-eabi-gcc -Os -std=c99 -ggdb3 -mthumb -mcpu=cortex-m4 -mfloat-abi=hard -mfpu=fpv4-sp-d16 -Wextra -Wshadow -Wimplicit-function-declaration -Wredundant-decls -Wmissing-prototypes -Wstrict-prototypes -fno-common -ffunction-sections -fdata-sections -DGIT_SHA=\"9fbd06c\" -DBUILD_TS=\"2022-08-02T09:30:14\" -Isrc -DVERBOSE=0 -std=gnu99 -mfloat-abi=hard -Wno-unused-parameter -Wno-unused-variable -Wno-unused-function -Os -DSTM32F446 -DSTM32F4xx -MD -Wall -Wundef -DSTM32F4 -I/home/billa/els/libopencm3/include  -o obj/src/convex_ext_l.o -c src/convex_ext_l.c
src/convex_ext_l.c:9:10: fatal error: libopencm3/cm3/dwt.h: No such file or directory
    9 | #include <libopencm3/cm3/dwt.h>
      |          ^~~~~~~~~~~~~~~~~~~~~~
compilation terminated.
make: *** [rules.mk:187: obj/src/convex_ext_l.o] Error 1
billa@billa:~/els$

hobbymachinist, 2022-08-02:
@kzali Is there a `/home/billa/els/libopencm3/include/libopencm3` folder ? I think that's what gcc is complaining about

kzali, 2022-08-02:
billa@billa:~$ cd libopencm3
billa@billa:~/libopencm3$ ls
COPYING.GPL3  COPYING.LGPL3  HACKING  HACKING_COMMON_DOC  Makefile  README.md  doc  els  include  ld  lib  locm3.sublime-project  mk  scripts  tests
billa@billa:~/libopencm3$ cd include
billa@billa:~/libopencm3/include$ ls
libopencm3  libopencmsis

yes the folders are there

hobbymachinist, 2022-08-02:
heh, `-I/home/billa/els/libopencm3/include` so that's wrong

it should be /home/billa/libopencm3, check your OPENCM3_DIR env variable

kzali, 2022-08-02:
Thanks will check that and give it a shot
Alas my terrible Linux skills.  Appreciate your help, I guess that's how
one learns!

On Tue, 2 Aug 2022, 10:50 am hobbymachinist, ***@***.***>
wrote:

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

kzali, 2022-08-02:
> heh, `-I/home/billa/els/libopencm3/include` so that's wrong
>
> it should be /home/billa/libopencm3, check your OPENCM3_DIR env variable

@hobbymachinist  Thanks cleaned the env variable's and export OPENCM3_DIR=$PWD/libopencm3
vola it worked like magic!!  Thanks to you learnt a lot today.
Cheers

Closed 2022-08-20.

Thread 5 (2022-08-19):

2 DRO and display issue

UberChmonya, 2022-08-19:
Hi, I really like your project! Is it possible to create an encoder for each axis (MPG) in the project? It would be very nice. I completely removed the mechanical control of the axes from the machine. Also, I could not find a display module for sale. What can replace it?

hobbymachinist, 2022-08-20:
Thanks.

Sorry, I don't plan on adding support for multiple MPG encoders - I need the extra pins for additional features I'm working on. You can customise the code to suit your needs though, but I most likely will not be able to add support for it.

>  I could not find a display module for sale. What can replace it?

Did you check AliExpress or eBay ? ILI9481 based 480x320 TFT modules are fairly common

e.g.
https://www.aliexpress.com/item/1984270730.html

AndreyFly007, 2022-09-05:
Good day friend.

> I need the extra pins for additional features I'm working on

Maybe there are details about which pins and interrupts will be occupied?

I started to repeat your device. I changed the printed circuit board, placed the connectors that are convenient for me. Aliexpress did not have the recommended screen. Therefore, the screen had to be ordered without an arduino shield. The screen will connect directly to the ELS, without a shield. Soon I will be able to share the printed circuit board (it remains to finish a few little things).
I would be very grateful if you could expand the list of which pins and interrupts will be used.

At the moment, to use the second MPG, I have used pins PC0, PC1, as well as an interrupt on PC0.
until the PCB is ordered, I have time to adjust the circuit for further compatibility with your project.

AndreyFly007, 2022-09-05:
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

hobbymachinist, 2022-09-05:
@AndreyFly007

I've left PC0, PC1, PC10, PC11, PH0, PH1 free for now. Rest are reserved, I might be able to free up some more pins after I change the board design to convert differential DRO signals to single ended.

The primary (MPG) encoder is used for menu selection and along with MPG for X and Z travel, I'd be interested to see how you're using 2 encoders in the user interface.

AndreyFly007, 2022-09-05:
> The primary (MPG) encoder is used for menu selection and along with MPG for X and Z travel, I'd be interested to see how you're using 2 encoders in the user interface.

the first MPG works without changes, menus, moving the Z axis. The second MPG will only be for the X axis.
My machine does not have mechanical manual movement handles. The Z and X axes can only be controlled electronically.

AndreyFly007, 2022-09-05:
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

hobbymachinist, 2022-09-05:
@AndreyFly007 I don't want to discourage you, but it looks like you've done extensive changes. I would pause and think about what you really want in the end. It sounds like conversational wizard with Linux CNC, Mach 4 or Acorn would be much better. You can do everything this project does and much more. You can also use 2 MPG wheels for dual axis control.

This project is quite experimental and I'm doing it for fun, you're more than welcome to do the same but in terms of investing time and money to get the features you're after the above mentioned options could be better.

hobbymachinist, 2022-09-05:
@AndreyFly007 See Kent's channel for how he's done it, https://www.youtube.com/watch?v=JdhNRhK3TCY. You can reach out to him to ask for tips if that's the route you want to take.

AndreyFly007, 2022-09-05:
I like your project. This project has great potential for development. Superficially looked through the code, found many interesting solutions for synchronizing the spindle with the feed. There is almost everything for working with Gcode, the only thing left is the parser procedure.
I know about all ready-made solutions (mach3, mach4, linux cnc), but they are not interesting to me. I love DIY projects. Your project is a great opportunity to plunge into the world of STM32.

hobbymachinist, 2022-09-05:
There's a lot of scope for improvement, especially with PWM and DMA but that will need remapping of GPIO pins. For what it's doing at the moment, it's good enough. I might revisit optimisations once I have all the basic features implemented.

AndreyFly007, 2022-09-07:
there is a very good example of Gcode parser on 2 axis on Github. For G0, G1, G2, G3 Gcode already has all the functions in your code. Code with a good description for Arduino, and can help you get started with GCode

[https://github.com/MarginallyClever/GcodeCNCDemo/tree/master/GcodeCNCDemo2Axis](url)

hobbymachinist, 2022-09-08:
@AndreyFly007 thanks, I'll take a look. There are couple of good options for GCode but I'm leaning towards a modified version of GRBL and a complete rewrite of the ELS functions to use the motion controller in GRBL. This would allow it to keep up with any newer versions of GRBL as a GCode processor, motion & stepper / servo controller allowing it to work with CAM post processors.

AndreyFly007, 2022-09-08:
I spent a lot of time looking for GRBL firmware for a lathe. None of them work with spindle synchronization. All I found is GRBL HAL, but even there it says that support for synchronization with the spindle is in test mode.
Прочитав много форумов, я пришел к выводу, что 90% операторов токарного станка пишут Gcode вручную в блокноте. для CNC токарного станка достаточно иметь G0, G1, G2, G3, G4, G32, G33, G76, G90, G91, G92. Для выполнения этих кодов в Вашей программе уже все есть. У Вас есть код для перемещения линейно и по радиусу, это G0, G1, G2, G3. Очень легко реализовать G4, это пауза. G32, G33, это нарезание резьбы. G76 это нарезание резьбы в цикле за несколько проходов. Остальные команды, это команды работы с системой координат.
Все CAM post processors настраиваются на Gcode поддерживаемый станком. 1 раз настроили CAM post processors и создавайте Gcode для своего станка на любые, даже очень сложные детали. Ваша прошивка в 1 шаге от CNC.

hobbymachinist, 2022-09-09:
There are a fair few issues to work out before I can be confident of using the motion controls for full GCode

1. linear xz movements aren't accurate, i.e. the final taper angles are incorrect.
2. the acceleration profiles are very naive, I'd like to get that fixed first.
3. fully automated threading loses DRO position at speeds over 400 rpm, not critical if you're not using closed loop backlash compensation but it's a deal breaker for me.
4. I'd like to have native tool radius compensation in the motion planner, but that's not a show stopper, most CAMs have this built-in
5. servo spindle control, possibly just PWM based to start with for constant sfm

Closed 2022-08-20.

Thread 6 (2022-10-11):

Are there compatible dev boards?

gerritv, 2022-10-11:
STM32's are rare at present, when they become available again are other version ok to use? I realized pin assignements might change but if it is STM32 based will that be ok? I think LPC1768 support in libopencm3 is not complete else I would ask about that as well.

hobbymachinist, 2022-10-11:
I initially wrote this to be compatible with both 103CB, 441RE and 446RE but ended up ditching the first 2 due to processing and gpio requirements. So at this stage unfortunately no and it looks like they're sold out everywhere until mid 2023, sorry. I am planning to redesign this sometime later this year or early next, I can look at other options then if the shortage persists.

hobbymachinist, 2022-10-11:
@gerritv if you're comfortable designing and building your own pcb, LCSC have some STM32F446RET6 in stock https://lcsc.com/search?q=stm32f446ret6

gerritv, 2022-10-12:
Thank you, I think I will work at being patient, some sites say November for the Nucleo.
(The RELS I am using is passable for now but look forward to moving to something decent soon. )

hobbymachinist, 2022-10-12:
@gerritv I wouldn't consider this anywhere close to implementations like ELSv4 Pro from Rocketronics. As noted in the documentation, this is very much experimental and fairly complex build to add to that. If you're looking to get a good ELS replacement, I'd strongly recommend the Rocketronics ELSv4 basic or pro. The BOM cost for this project is pretty close to the ELSv4 basic pricing anyways, and that has professional support and nice features such as tool radius compensation.

If you're like me and like tinkering soldier on :)

gerritv, 2022-10-12:
I don't mind tinkering. Even with the Euro at a better rate of conversion than usual, it is too much $ all at once.
Presently I use RELS7e2. It works but there are some issues with large thread pitches, and also with small ones. The code is not pretty. The hard work IMO is adding the X stepper drive, and with both steppers in place, swapping controllers is not a big issue.

Would one of the M4 based Nucleo's work?

hobbymachinist, 2022-10-12:
M4 based Nucleos ? You mean https://www.mikroe.com/mini-stm32f4 ? It may work, I'll have to go through the datasheet for STM32F415RG but STM32s are generally pin compatible within one family but the peripheral / AF config might be slightly different.

gerritv, 2022-10-12:
I was thinking along these lines: https://www.digikey.ca/en/products/detail/stmicroelectronics/NUCLEO-L452RE-P/7380300

hobbymachinist, 2022-10-12:
L452s are low power, so run much slower. It's going to struggle handling the TFT and other real time tasks at the same time. I could get it barely running without jitters on the 411RE that runs at 125MHz. I haven't spent a lot of time optimising the control loop, but the LCD refreshes are expensive even with DMA.

gerritv, 2022-10-12:
Can you confirm that this is The One please? yesterday there were 0, now.... https://www.mouser.ca/ProductDetail/STMicroelectronics/NUCLEO-F446RE

hobbymachinist, 2022-10-12:
STM32F429ZI, yeah that'd work. It's Nucelo-144 though, so you'd have to make your own break out board in addition to customising the gpio config to suit it but doable.

hobbymachinist, 2022-10-12:
mouser Australia has stock, yes it's the part number you have https://au.mouser.com/ProductDetail/511-NUCLEO-F446RE

gerritv, 2022-10-12:
it is for evaluatoin of STM32F446RET6 so I will order 2 .
thank you for your patience and help :-)

hobbymachinist, 2022-10-12:
Haha, I'll order an extra board for myself. Thanks for scouring the interwebs :laughing:

gerritv, 2022-10-14:
Nucleo boards arrived, waiting on @kzali for mailing costs for a set of breakout boards. Would love to get a second set as I am buiding one for myself, one for a friend.

AndreyFly007, 2022-10-23:
> but the LCD refreshes are expensive even with DMA.

display less frequently
Clockwise / Counter clockwise direction of spindle and RPM. Chuck icon is shown when RPM = 0

remove from screen:
Angular position of the spindle in degrees. This can be used for any indexing functions.
Pulse counter, this is a function of the encoder PPR and wraps around. Threading operations synchronise to this value.

Another option is to install a cheap processor for displaying. Send the necessary data with ELS, and let the cheap processor redraw the screen

Closed 2022-10-11.

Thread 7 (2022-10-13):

Using Platformio and Kicad 6.0

gerritv, 2022-10-13:
I forked the repo and have it compiled using Platformio as a build system. (I use VSCode and Pio for everything)

Are you interested in a pull request?
https://github.com/gerritv/HM-els

KiCAD wanted to 'rescue' some outlines.
Platformio needed its .ini file
A few code changes due to constants being renamed in libopencm3 for the f4. e.g. in clock.c, it is now RCC_CFGR_HPRE_DIV_NONE, previously it was RCC_CFGR_HPRE_NODIV

hobbymachinist, 2022-10-13:
> I forked the repo and have it compiled using Platformio as a build system. (I use VSCode and Pio for everything)

I would recommend creating a separate repo with els vendored and putting your local IDE / build config in that repo. This keeps the upstream clean and allows you to customise your build / dev environment.

> KiCAD wanted to 'rescue' some outlines.

Yes, I'm in the middle of migrating the project to Kicad 6. I'll push some updates soon.

> A few code changes due to constants being renamed in libopencm3 for the f4. e.g. in clock.c, it is now > RCC_CFGR_HPRE_DIV_NONE, previously it was RCC_CFGR_HPRE_NODIV

I'll look into that as well, thanks. I'll have to test with new version of libopencm3, I might have to consider pinning libopencm3 versions to avoid build issues.

hobbymachinist, 2022-10-13:
I've pushed the initial Kicad 6.0 migration / changes over. I haven't updated the add on daughter boards, but that should be straightforward.

https://github.com/libopencm3/libopencm3/blob/master/include/libopencm3/stm32/f4/rcc.h#L228  that's still RCC_CFGR_HPRE_DIV_NONE

are you using a different version / tag ?

hobbymachinist, 2022-10-13:
@gerritv Why have you removed the symlinks ?

https://github.com/hobbymachinist/els/compare/main...gerritv:HM-els:main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

gerritv, 2022-10-13:
I changed the clock.c file from RCC_CFGR_HPRE_NODIV to RCC_CFGR_HPRE_DIV_NONE. ..._DIV2 becomes DIV_2 etc. I'm assumin gthe libopencm3 is newest in Platformio.

gerritv, 2022-10-13:
`"I would recommend creating a separate repo with els vendored and putting your local IDE / build config in that repo. This keeps the upstream clean and allows you to customise your build / dev environment.`
I'll figure out how to do that over the next day or so, tku.

hobbymachinist, 2022-10-13:
libopencm3 link above is from their github repo, it's the latest. I suspect the version in platformio is old (at least by 2yrs). I recommend using the latest version.

gerritv, 2022-10-13:
> @gerritv Why have you removed the symlinks ?
>
> [main...gerritv:HM-els:main#diff-a37ff317ec9d68c5ca74e2471f6b7e428bf47a510c81a34918cd7cbe19e5008eR1](https://github.com/hobbymachinist/els/compare/main...gerritv:HM-els:main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)

I was getting dup references on the link, but  may have solved that another way. Also  I have never come across that construct before  so 'solved it' :-)

hobbymachinist, 2022-10-13:
you need to exclude the platform files, see the Makefile for guidance

https://github.com/hobbymachinist/els/blob/main/Makefile#L5-L6

gerritv, 2022-10-13:
> libopencm3 link above is from their github repo, it's the latest. I suspect the version in platformio is old (at least by 2yrs). I recommend using the latest version.

Platformio's version is same as what you listed, the code in clock.c then was old? clock.c was using NODIV.

gerritv, 2022-10-13:
> you need to exclude the platform files, see the Makefile for guidance
>
> https://github.com/hobbymachinist/els/blob/main/Makefile#L5-L6

I excluded them in platformio.ini, but tft.c gives me this error:

src\tft\tft.c:1:9: error: expected '=', ',', ';', 'asm' or '__attribute__' before '/' token
 platform/tft_opencm3_stm32fx.c"

I'll dig into that tomorrow, its late up here.

hobbymachinist, 2022-10-13:
> https://github.com/libopencm3/libopencm3/blob/master/include/libopencm3/stm32/f4/rcc.h#L228 that's still RCC_CFGR_HPRE_DIV_NONE

I meant to say that's still RCC_CFGR_HPRE_NODIV in the latest libopencm3 and the constant in src/clock.c is correct.  'night.

gerritv, 2022-10-13:
A total lack of versioning of libopencm3 made this extra challenging, I guess ppl forgot how to incorement file version #'s :-( I found a solution though (for the benefit of others who run into this issue): https://community.platformio.org/t/compiler-doesnt-find-function-definition-libopencm3/25795/5 . This approach would make a configuration manager freak out but it works. And Platformio is behind in updating libraries. (Given where they are in the world it is understandable.)

So now back to the symlink in tft.c. Can you give me a lead on where to read about this construct? Searching the web for anything symlink only returns stuff about file systems.

hobbymachinist, 2022-10-13:
> So now back to the symlink in tft.c. Can you give me a lead on where to read about this construct? Searching the web for anything symlink only returns stuff about file systems.

I've pushed some changes to remove the symlinks, they're essentially symbolic pointers in the file system to actual files. You should be able to compile them as is now.

hobbymachinist, 2022-10-13:
it's a bit late here, I'll check back tomorrow.

gerritv, 2022-10-13:
Thank you for your help and patience.
Ok, all solved. Tku for removing the symlink, not common on windows. I thought it was some magic need C standard thing :-)

By adding a platfrom.ini file and a python script to get output from git rev-parse, I now have a clean build.

I can do a pull request for you to add those 2 files, or I can keep it local to my PC.

For others:
platformio.ini:
[env:nucleo_f446re]
platform_packages = framework-libopencm3 @ https://github.com/larmicfre/libopencm3.git
platform = ststm32
framework = libopencm3
board = nucleo_f446re
build_flags =
    !python git_rev_macro.py
    -Wno-unused-variable
    -Wno-unused-function

git_rev_macro.py:
import subprocess

revision = (
    subprocess.check_output(["git", "rev-parse", "HEAD"])
    .strip()
    .decode("utf-8")
)
print("'-DGIT_SHA=\"%s\"'"%revision)

hobbymachinist, 2022-10-13:
If I add it to upstream here, I'll have to maintain it and make sure I don't commit breaking changes. Since I don't use platformio or vscode, it might be something better suited for you to maintain locally.

Closed 2022-10-13.

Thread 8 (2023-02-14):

Non integer steps-per-mm

Jgr2023, 2023-02-14:
First of all, many thanks for all your work on this project!

I'm looking at fitting the ELS to a lathe with a 6mm pitch leadscrew and with a 200 steps/rev stepper on the z-axis.

This gives a non-integer steps-per-mm.

I trying to understand if this will cause an accumulating error in open loop.

I think I can see a solution by storing two numbers instead of one number (a number of steps and a corresponding mm of travel), but that may be getting a bit ahead of myself.

I look forward to hearing your thoughts.

Thanks,
J.

hobbymachinist, 2023-02-14:
Thanks. The best option is to add a 1.5x pulley reduction from your stepper to the leadscrew, so you get an even number. 200 steps = 4mm, 50 steps per mm. No need to make the software complicated and as an added benefit you get extra torque.

Closed 2023-02-14.

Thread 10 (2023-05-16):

LCD ?

beyma1, 2023-05-16:
Brak możliwości zakupu wyświetlacza ILI9481. Zakupiłem ILI9486 oraz ILI9488, na żadnym z nich nic się nie wyświetla

hobbymachinist, 2023-05-17:
Sorry, I don't understand Polish but I assume you're asking if it will work with ILI9486 or ILI9488. It will not, you need to write a new software driver for those. I don't have those LCDs to test so I can't help you at this time, sorry.

hobbymachinist, 2023-05-19:
I purchased a ILI9488 display, I'll have to wait a month or so for it to arrive and I can take a look at adding support for it once I have it.

beyma1, 2023-05-20:
Dzieki.... fajnie by bylo gdyby sie udalo przerobic kod by els pracowal pod ili9488. W oryginalnym projekcie wykorzystany jest ili9481 ktory praktycznie jest juz nie dostępny. Ostatnio udalo mi sie znalezc u chinczyka ale wersja z dotykiem. Zamowilem go i tez przyjdzie za jakis miesiąc hehe. Ciekawe czy ten wyswietlacz to naprawdę przyjdzie ili9481 albo jakis fake.... czas pokaże. pozdrawiam

Thanks .... it would be nice if you could change the code so that els would work under ili9488. The original project uses ili9481, which is practically no longer available. Recently, I managed to find a Chinese version, but with a touch. I ordered it and it will arrive in about a month hehe. I wonder if this display will really come ili9481 or some fake .... time will tell. Regards

beyma1, 2023-05-21:
"Refer to the GPIO pins listed below, the solder bridges for these pins should be setup correctly. See Nucleo 446RE documentation UM1724, Section 6.9 on Solder Bridges."
Could you please explain which jumpers are you talking about? Do these jumpers also affect the operation of the display?

hobbymachinist, 2023-05-21:
https://github.com/hobbymachinist/els/blob/main/docs/els.md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

Hope that helps

beyma1, 2023-05-21:
I made all the jumpers as you described .... However, I missed one SB51 jumper. After its disassembly, ELS works on both displays ... ILI9486 and ILI9488

beyma1, 2023-05-21:
Although the colors are different than yours with the ILI9481 display, but the fact WORKS :)

hobbymachinist, 2023-05-21:
> However, I missed one SB51 jumper.

@beyma1 You mean SB21 ? SB51 is for PC0, which is unused. Glad you got it working, the colors are hardcoded to ILI9481, I'll have a look at updating them for ILI9488 when I get my LCD.  If you can share a video or some photos once you got the ELS working, I'd appreciate it :)

beyma1, 2023-05-23:
Of course, I meant the SB21 jumper (my spelling error .... Already corrected)

hobbymachinist, 2023-05-23:
You're nearly there, hope you get it working soon and are happy with it :)

beyma1, 2023-05-25:
I'm already satisfied... The mere fact that the lcd lights up makes me happy. Can the keyboard be replaced with something else? I don't like to spend so much money on a dedicated keyboard that was used in the project. Maybe there are alternatives?

hobbymachinist, 2023-05-25:
You can get a cheap PS/2  keypad and use that. +5V, GND, Data (PC5) and Clock (PC4) from the keypad should go to the keypad connector

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

hobbymachinist, 2023-05-26:
yeah that's not too hard. PS/2 19-20 key plastic keypads are very cheap $15-20, if you want to save yourself the trouble. You can remove the standard enclosure and 3D print a mounting plate for it. Only change needed to firmware would be changes to the scan codes in constants.h

hobbymachinist, 2023-05-30:
Did you have to change any initialisation sequence / code for ILI9488 and ILI9486 ? I received a ILI9488 today, I don't think they work out of the box.

beyma1, 2023-05-30:
The displays worked without any modifications. Today I received the display and as it is with the Chinese instead of ILI9481 I received ILI9488 ehh. This display works too. So theoretically all these displays are interchangeable, only the colors are different (as you can see in the photos I posted earlier)

hobbymachinist, 2023-05-30:
haha,  I got 2 that are supposed to be ILI9488. They don't work at all, I'm not sure I want to try debugging this :)

I'll have a look at the datasheet when I find time and investigate. Re. colours, the color byte order might be different that what the ILI9481 driver uses (BGR). You can try swapping them.

hobbymachinist, 2023-05-31:
@beyma1 do you have a link to where you purchased ILI9488 from ? thanks

hobbymachinist, 2023-05-31:
@beyma1 I got ILI9488 working, looks like the command set is entirely compatible, but I need some time to review the ILITEK datasheet to confirm that the initialisation sequence is not going to affect the display in the long term.

https://github.com/hobbymachinist/els/blob/main/Makefile#L25   comment out the default ILI9481, uncomment ILI9488 and give it a try. Colors look fine to me, it's mostly a controller timing issue. ILI9488 seems slower, so needs additional delay to process signal transitions.

hobbymachinist, 2023-06-03:
updated ILI9488 initialisation, please use the latest driver code.

beyma1, 2023-06-15:
I checked and the new codes work. And the funniest thing is that I have two ili9486 and two ili9488 displays (from two different suppliers) and only one of them works .... The Chinese man sold me some broken displays. Well, it's hard. In some time I will try to handle the keyboard on arduino nano, the board is already made, just solder and program it (if I find time). Recently, I've also been thinking about replacing this display with a DWIN with a touch panel .... It would also be nice to implement this driver ... But it will probably stay in the dream phase

hobbymachinist, 2023-06-15:
This is where I got the original ILI9481 and the ILI9488s from https://www.aliexpress.com/item/1005001288341298.html

Seems reliable.

Touchpanels are problematic in the machine shop, especially capacitive touch (due to electrical noise), oil and dirt in the fingers also pose an issue. I wouldn't recommend.

Closed 2023-05-17.

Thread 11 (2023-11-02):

Freeing PA4, PA5

pantonov2, 2023-11-02:
First of course congrats on the great job well done!!

I'm considering this project for a small lathe where I'd add a spindle control via analog signal. What would be most effective way to free one DAC output where pin is currently in use for TFT data? Had some look at source where a comment stays stating that pin number is ignored...

Another approach would be to generate a PWM and convert it to voltage. I'm a little bit reluctant to do so when a DAC is there.

I'm also considering adding HW limits and getting rid of the overpriced keypad while reducing number of keys/buttons mostly because of space considerations.

Thanks in advance!

hobbymachinist, 2023-11-16:
It would require a bit of a rewrite of the tft code and the reason to use contiguous pins is to reduce the bit operations in data transfer and thereby reduce refresh latency - this has an impact on time critical operations e.g. threading.

Feel free to experiment with it, my long term plan is to use pwm since I plan to replace the VFD with a servo drive. It might be easier to add an external i2c or spi dac, or even just use pwm with an appropriate low pass filter.

It is open source, modify the code and design as it suits you but I wouldn't be interested in merging any breaking changes upstream since this is mostly a worklog / archive of my setup that could be of use as a starting point for others.

Closed 2023-11-16.

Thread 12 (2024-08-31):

Taper cutting accuracy

klandrith, 2024-08-31:
Hello,
I have watched all your videos and read all of the documentation on this ELS. In one of your videos you mentioned that the taper cutting accuracy was less than ideal, but you were hopeful that closed loop linear scale feedback would alleviate this.

I haven't found any mention of how it ended up working out. I am considering outfitting my Harrison M300 lathe that is missing it's factory taper attachment with this ELS to add that functionality as well as other goodies. Any help would be appreciated, and thank you for the cool project.

hobbymachinist, 2024-08-31:
tl;dr without good quality ballscrew conversion, it's not precise but I've got acceptable results with conservative cuts and then polishing / grinding off high spots to finish.

If you're cutting tapers with the top / compound slide, then the accuracy of the taper is only dependent on the linear accuracy of the dovetail and gibs which would be very good. Even with closed loop setup, ELS only compensates for backlash at the start of the cut at the moment.  So the accuracy is now a function of the the accuracy of the following:

1. Z leadscrew
2. Z halfnuts
3. X leadscrew
4. X halfnuts
5. cross slide dovetail & gibs

I've tried continuous compensation with varying results, none satisfactory because the DRO scales themselves have errors of up to +/- 5um. If I need a taper turned with high precision, I still bring out my compound slide but I'm planning to make a custom taper cutting attachment with linear rails in the future.

hobbymachinist, 2024-08-31:
>  I am considering outfitting my Harrison M300 lathe that is missing it's factory taper attachment with this ELS to add that functionality as well as other goodies.

If you're comfortable tinkering with electronics and firmware go for it, otherwise something like https://www.rocketronics.de/shop/en/controls/lathecontroller/ would be a better option.

Closed 2024-08-31.

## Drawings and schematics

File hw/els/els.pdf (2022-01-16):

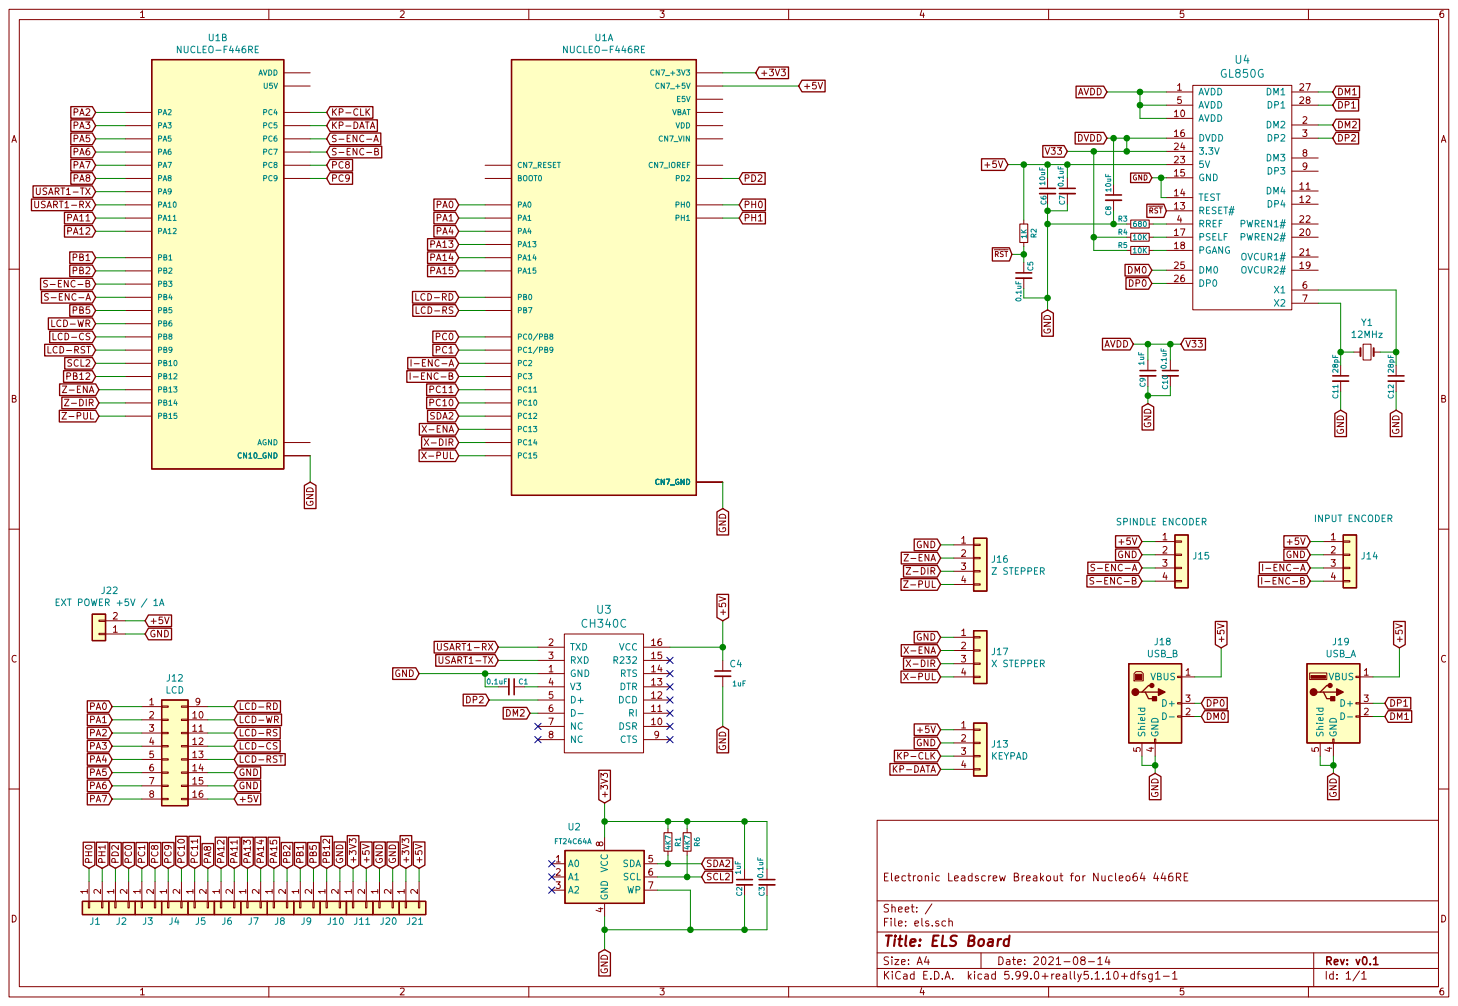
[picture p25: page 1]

4 SDA 5 SCL 6 WP 7 VCC

File: els.sch Sheet: / Electronic Leadscrew Breakout for Nucleo64 446RE

Id: 1/1 Title: ELS Board

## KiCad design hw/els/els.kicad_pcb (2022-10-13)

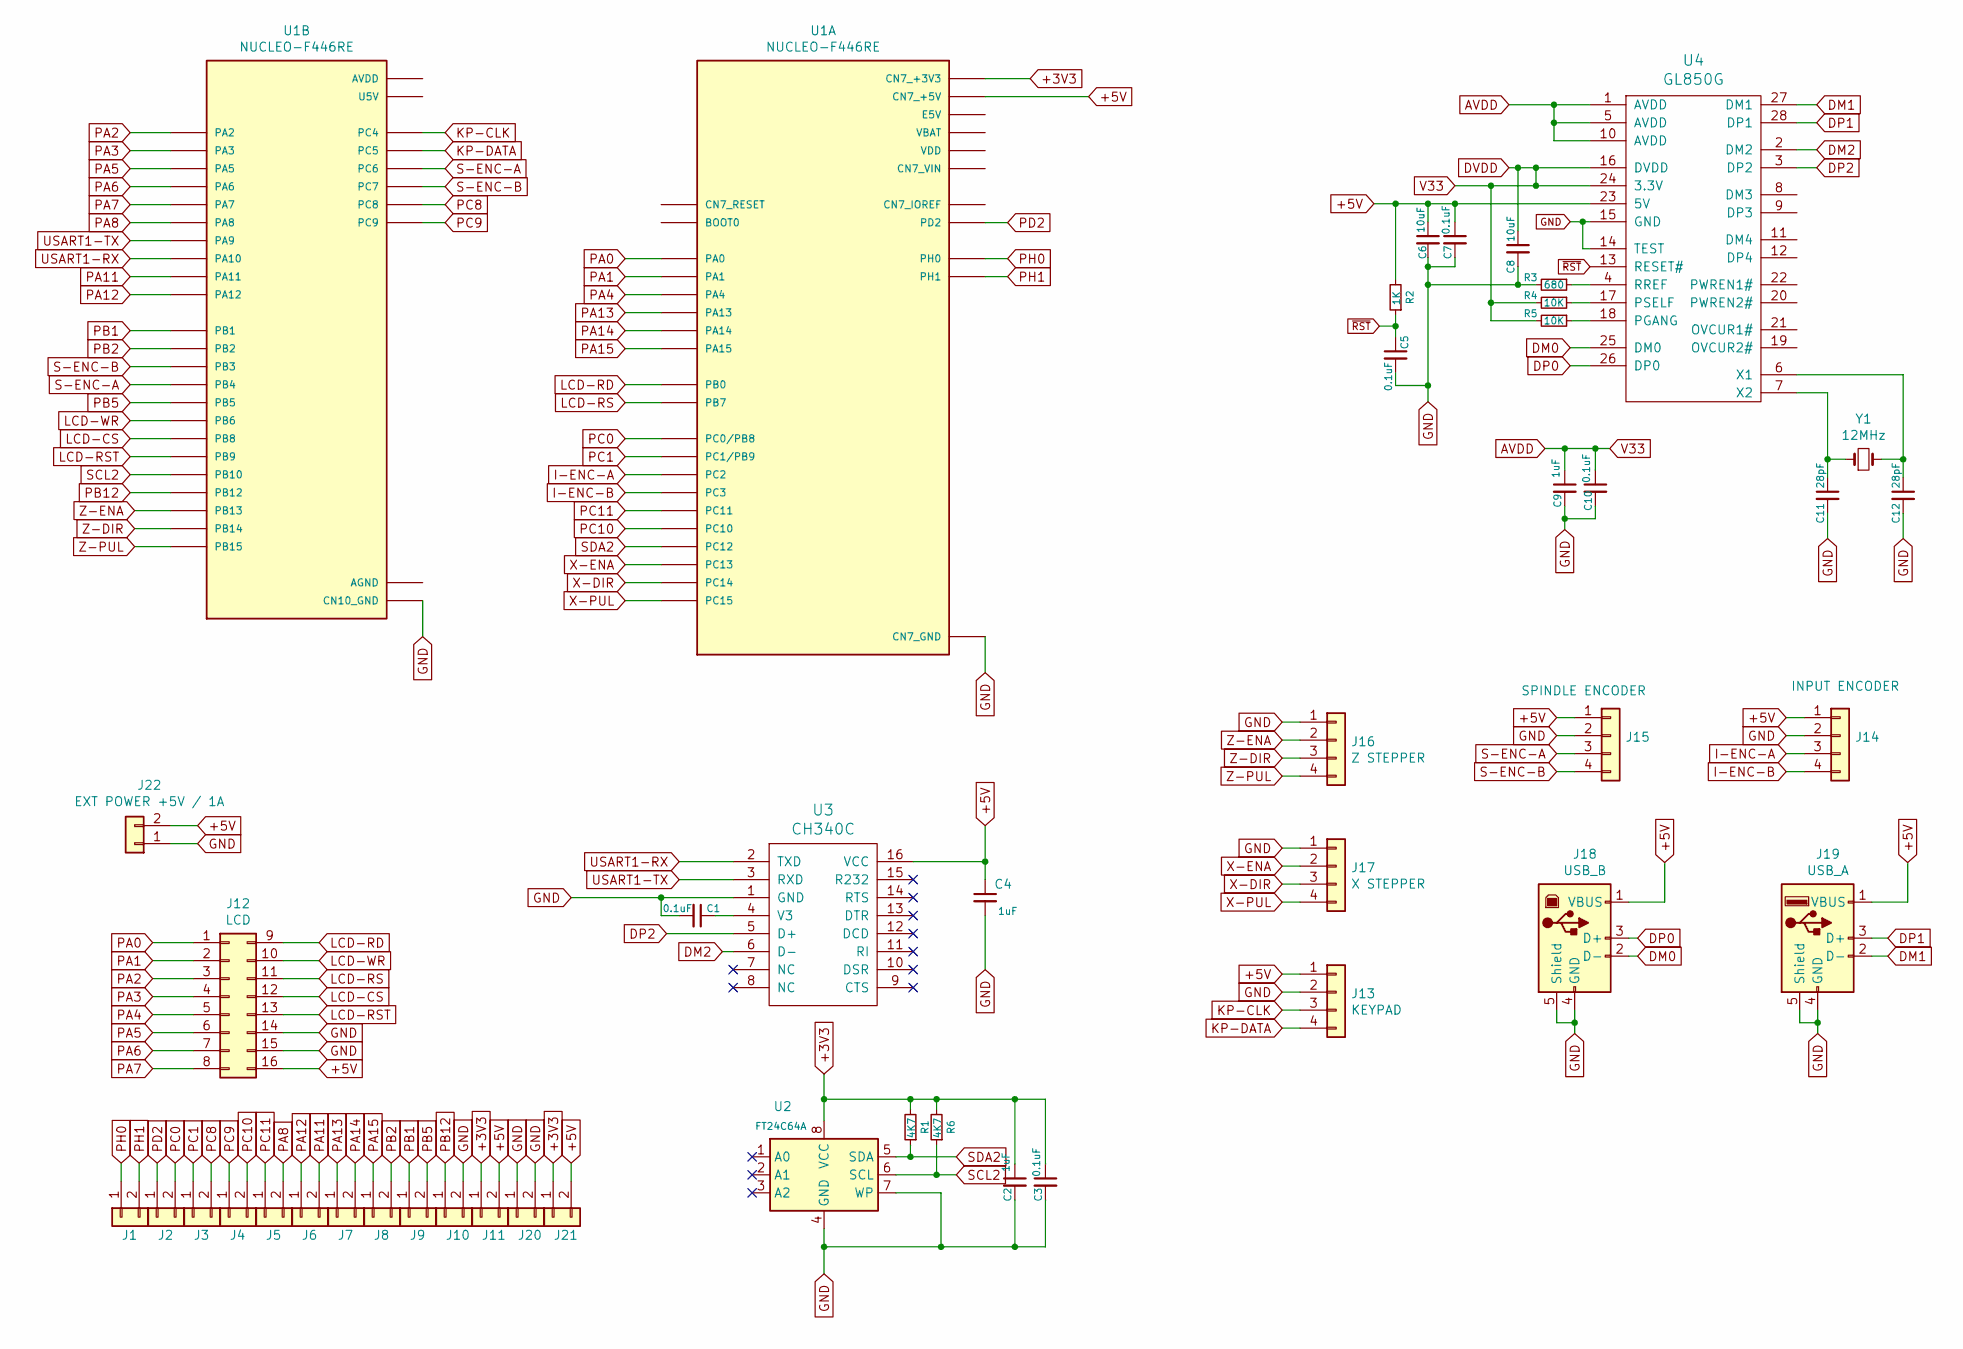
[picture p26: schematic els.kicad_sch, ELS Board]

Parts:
C1, C3, C5, C7, C10: 0.1uF; C_0805_2012Metric_Pad1.15x1.40mm_HandSolder
C2, C4, C9: 1uF; C_0805_2012Metric_Pad1.15x1.40mm_HandSolder
C6, C8: 10uF; C_0805_2012Metric_Pad1.15x1.40mm_HandSolder
C11, C12: 28pF; C_0805_2012Metric_Pad1.15x1.40mm_HandSolder
J1, J2, J3, J4, J5, J6, J7, J8, J9, J10, J11, J20, J21: Conn_01x02; TerminalBlock_bornier-2_P5.08mm
J12: LCD; IDC-Header_2x08_P2.54mm_Vertical
J13: KEYPAD; PinSocket_1x04_P2.54mm_Vertical
J14: INPUT ENCODER; PinSocket_1x04_P2.54mm_Vertical
J15: SPINDLE ENCODER; PinSocket_1x04_P2.54mm_Vertical
J16: Z STEPPER; PinSocket_1x04_P2.54mm_Vertical
J17: X STEPPER; PinSocket_1x04_P2.54mm_Vertical
J18: USB_B; USB_B_OST_USB-B1HSxx_Horizontal
J19: USB_A; USB_A_CONNFLY_DS1095-WNR0
J22: EXT POWER +5V / 1A; TerminalBlock_bornier-2_P5.08mm
R1, R6: 4K7; R_0805_2012Metric_Pad1.15x1.40mm_HandSolder
R2: 1K; R_0805_2012Metric_Pad1.15x1.40mm_HandSolder
R3: 680; R_0805_2012Metric_Pad1.15x1.40mm_HandSolder
R4, R5: 10K; R_0805_2012Metric_Pad1.15x1.40mm_HandSolder
U1: NUCLEO-F446RE; MODULE_NUCLEO-F446RE; PARTREV 13
U2: FT24C64A; SO-8_5.3x6.2mm_P1.27mm
U3: CH340C; SOIC-16_3.9x9.9mm_P1.27mm
U4: GL850G; SSOP-28_5.3x10.2mm_P0.65mm
Y1: 12MHz; Crystal_HC49-4H_Vertical

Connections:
+3V3: C2.1, C3.1, J11.1, J21.1, R1.2, R6.2, U1.CN7_16 (CN7_+3V3), U2.8 (VCC)
+5V: C4.1, C6.1, C7.1, J11.2, J12.16, J13.1, J14.1, J15.1, J18.1 (VBUS), J19.1 (VBUS), J21.2, J22.2, R2.2, U1.CN7_18 (CN7_+5V), U3.16 (VCC), U4.23 (5V)
AVDD: C8.1, C9.1, C10.1, R4.2, R5.2, U4.1 (AVDD), U4.5 (AVDD), U4.10 (AVDD), U4.16 (DVDD), U4.24 (3.3V)
DM0: J18.2 (D-), U4.25 (DM0)
DM1: J19.2 (D-), U4.27 (DM1)
DM2: U3.6 (D-), U4.2 (DM2)
DP0: J18.3 (D+), U4.26 (DP0)
DP1: J19.3 (D+), U4.28 (DP1)
DP2: U3.5 (D+), U4.3 (DP2)
GND: C1.2, C2.2, C3.2, C4.2, C5.2, C6.2, C7.2, C8.2, C9.2, C10.2, C11.2, C12.2, J10.2, J12.14, J12.15, J13.2, J14.2, J15.2, J16.1, J17.1, J18.4 (GND), J18.5 (Shield), J19.4 (GND), J19.5 (Shield), J20.1, J20.2, J22.1, R3.2, U1.CN7_8 (CN7_GND), U1.CN7_19 (CN7_GND), U1.CN7_20 (CN7_GND), U1.CN7_22 (CN7_GND), U1.CN10_9 (CN10_GND), U1.CN10_20 (CN10_GND), U2.4 (GND), U2.7 (WP), U3.1 (GND), U4.14 (TEST), U4.15 (GND); also elsewhere on the board
I-ENC-A: J14.3, U1.CN7_35 (PC2)
I-ENC-B: J14.4, U1.CN7_37 (PC3)
KP-CLK: J13.3, U1.CN10_34 (PC4)
KP-DATA: J13.4, U1.CN10_6 (PC5)
LCD-CS: J12.12, U1.CN10_3 (PB8)
LCD-RD: J12.9, U1.CN7_34 (PB0)
LCD-RS: J12.11, U1.CN7_21 (PB7)
LCD-RST: J12.13, U1.CN10_5 (PB9)
LCD-WR: J12.10, U1.CN10_17 (PB6)
unnamed: C1.1, U3.4 (V3)
unnamed: C11.1, U4.7 (X2), Y1.1
unnamed: C12.1, U4.6 (X1), Y1.2
unnamed: R3.1, U4.4 (RREF)
unnamed: R4.1, U4.17 (PSELF)
unnamed: R5.1, U4.18 (PGANG)
PA0: J12.1, U1.CN7_28 (PA0)
PA1: J12.2, U1.CN7_30 (PA1)
PA2: J12.3, U1.CN10_35 (PA2)
PA3: J12.4, U1.CN10_37 (PA3)
PA4: J12.5, U1.CN7_32 (PA4)
PA5: J12.6, U1.CN10_11 (PA5)
PA6: J12.7, U1.CN10_13 (PA6)
PA7: J12.8, U1.CN10_15 (PA7)
PA8: J5.2, U1.CN10_23 (PA8)
PA11: J6.2, U1.CN10_14 (PA11)
PA12: J6.1, U1.CN10_12 (PA12)
PA13: J7.1, U1.CN7_13 (PA13)
PA14: J7.2, U1.CN7_15 (PA14)
PA15: J8.1, U1.CN7_17 (PA15)
PB1: J9.1, U1.CN10_24 (PB1)
PB2: J8.2, U1.CN10_22 (PB2)
PB5: J9.2, U1.CN10_29 (PB5)
PB12: J10.1, U1.CN10_16 (PB12)
PC0: J2.2, U1.CN7_38 (PC0/PB8)
PC1: J3.1, U1.CN7_36 (PC1/PB9)
PC8: J3.2, U1.CN10_2 (PC8)
PC9: J4.1, U1.CN10_1 (PC9)
PC10: J4.2, U1.CN7_1 (PC10)
PC11: J5.1, U1.CN7_2 (PC11)
PD2: J2.1, U1.CN7_4 (PD2)
PH0: J1.1, U1.CN7_29 (PH0)
PH1: J1.2, U1.CN7_31 (PH1)
S-ENC-A: J15.3, U1.CN10_4 (PC6), U1.CN10_27 (PB4)
S-ENC-B: J15.4, U1.CN10_19 (PC7), U1.CN10_31 (PB3)
SCL2: R6.1, U1.CN10_25 (PB10), U2.6 (SCL)
SDA2: R1.1, U1.CN7_3 (PC12), U2.5 (SDA)
USART1-RX: U1.CN10_33 (PA10), U3.2 (TXD)
USART1-TX: U1.CN10_21 (PA9), U3.3 (RXD)
X-DIR: J17.3, U1.CN7_25 (PC14)
X-ENA: J17.2, U1.CN7_23 (PC13)
X-PUL: J17.4, U1.CN7_27 (PC15)
Z-DIR: J16.3, U1.CN10_28 (PB14)
Z-ENA: J16.2, U1.CN10_30 (PB13)
Z-PUL: J16.4, U1.CN10_26 (PB15)
~RST: C5.1, R2.1, U4.13 (RESET#)

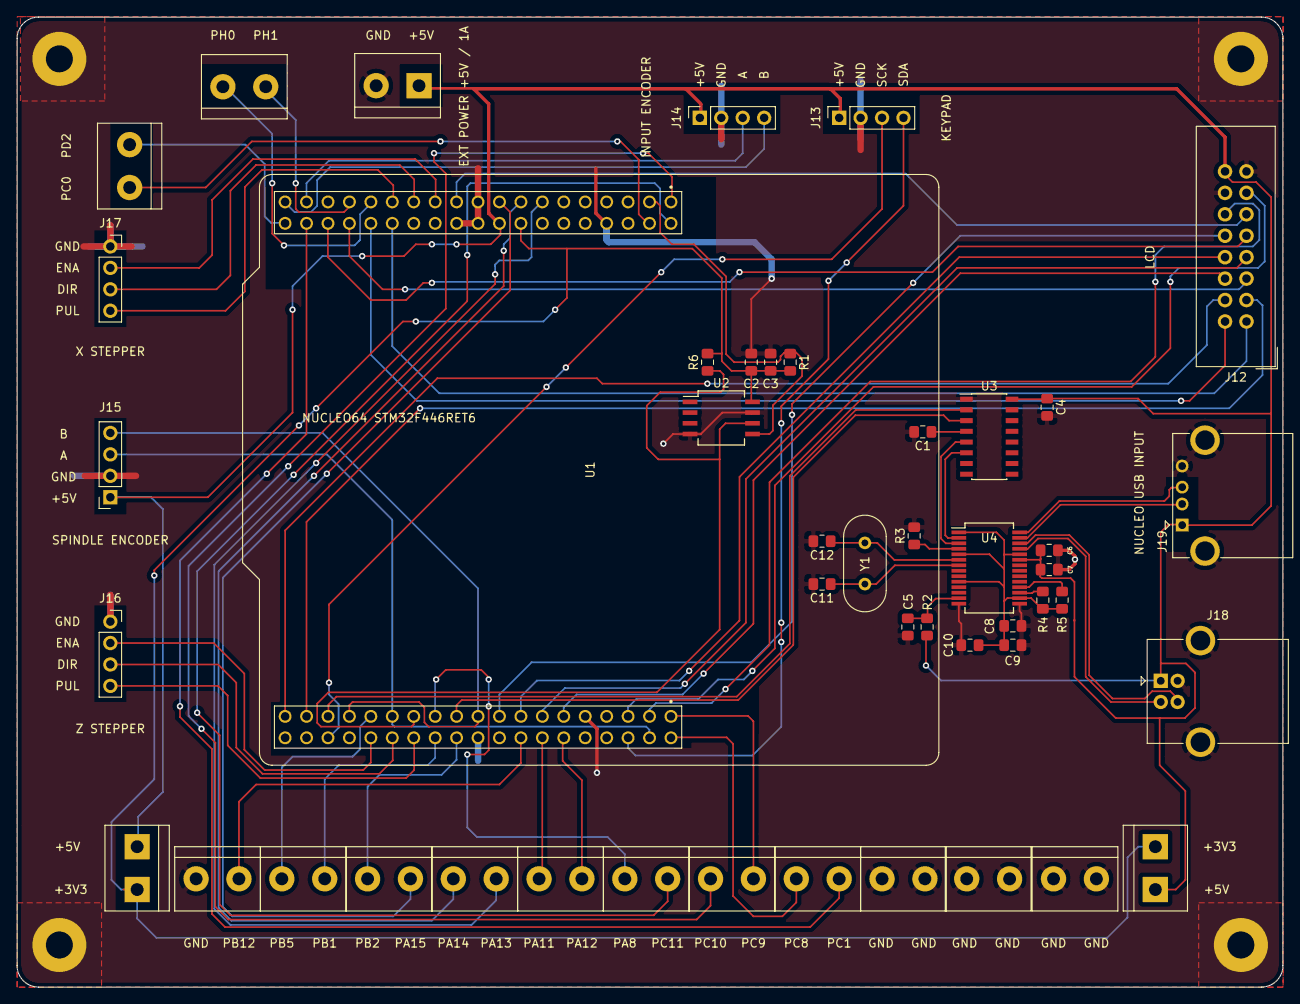
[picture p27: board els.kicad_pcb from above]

Board: 2 copper layers, 150.0 x 114.9 mm, 47 parts (0 on the bottom side), 65 nets.

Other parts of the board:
J20#2, J20#3: Conn_01x02; TerminalBlock_bornier-2_P5.08mm

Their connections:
GND: J20#2.1, J20#2.2, J20#3.1, J20#3.2; also elsewhere on the board

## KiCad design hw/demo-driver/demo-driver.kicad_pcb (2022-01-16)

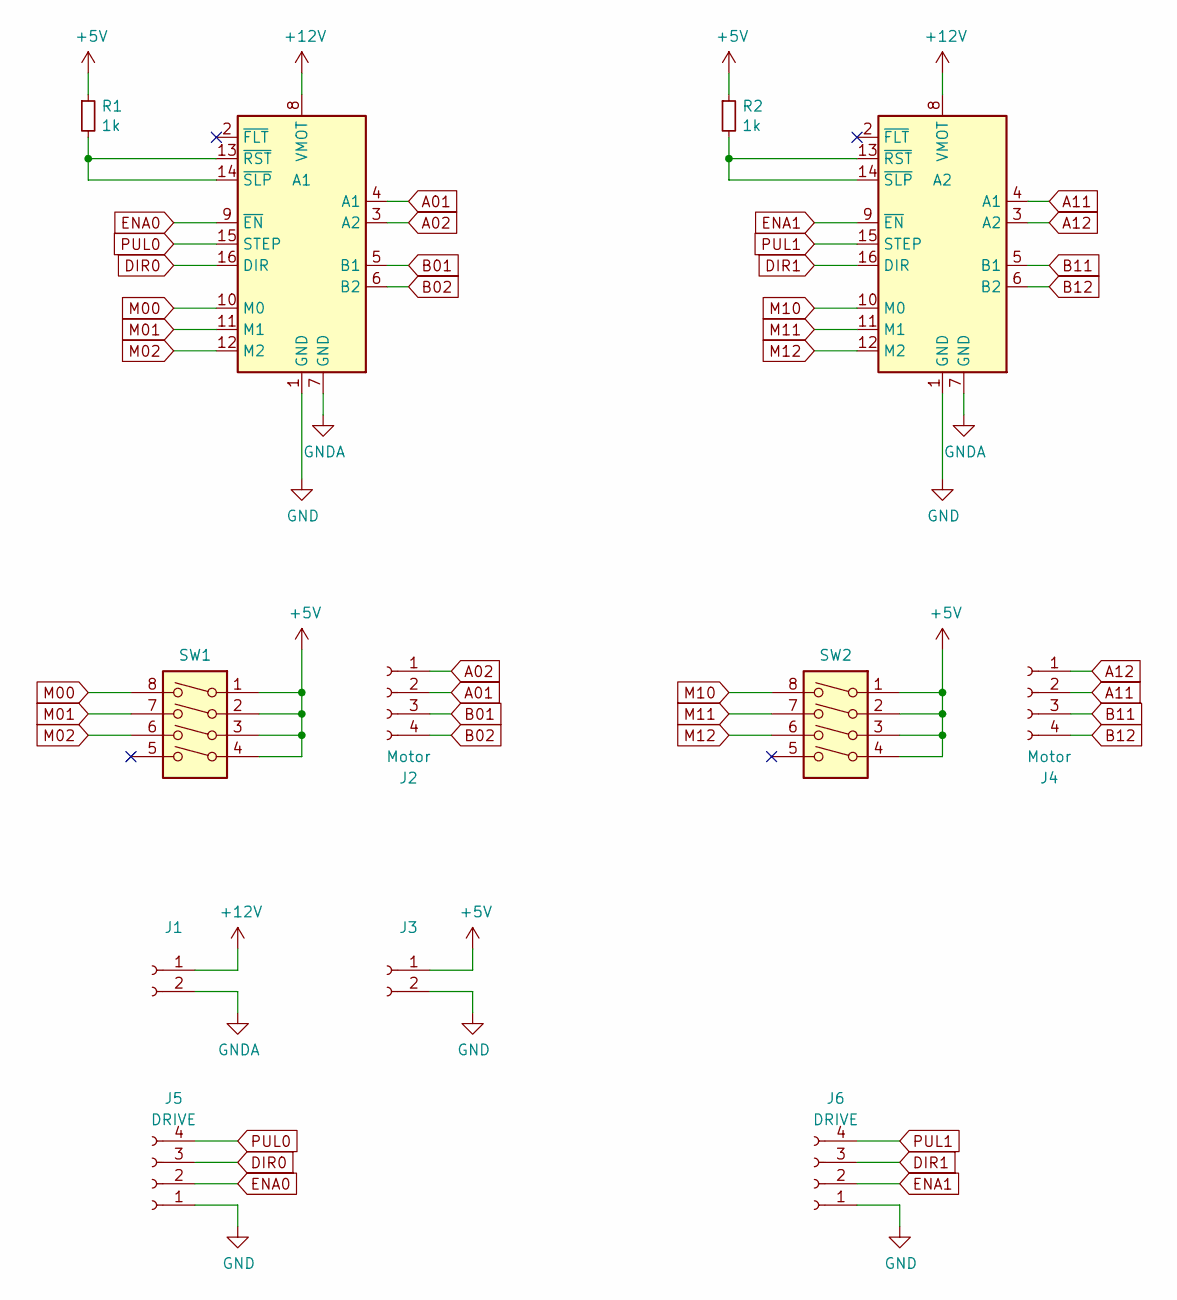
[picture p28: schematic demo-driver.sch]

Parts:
A1, A2: Pololu_Breakout_DRV8825; Pololu_Breakout-16_15.2x20.3mm
J1: VMOTOR; TerminalBlock_bornier-2_P5.08mm
J2, J4: Motor; PinSocket_1x04_P2.54mm_Horizontal
J3: VLOGIC; TerminalBlock_bornier-2_P5.08mm
J5, J6: DRIVE; PinSocket_1x04_P2.54mm_Horizontal
R1, R2: 1k; R_0805_2012Metric_Pad1.15x1.40mm_HandSolder
SW1, SW2: MICROSTEP; SW_DIP_SPSTx04_Slide_9.78x12.34mm_W7.62mm_P2.54mm

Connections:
+5V: J3.1, R1.1, R2.1, SW1.1, SW1.2, SW1.3, SW1.4, SW2.1, SW2.2, SW2.3, SW2.4
+12V: A1.8 (VMOT), A2.8 (VMOT), J1.1
A01: A1.4 (A1), J2.2
A02: A1.3 (A2), J2.1
A11: A2.4 (A1), J4.2
A12: A2.3 (A2), J4.1
B01: A1.5 (B1), J2.3
B02: A1.6 (B2), J2.4
B11: A2.5 (B1), J4.3
B12: A2.6 (B2), J4.4
DIR0: A1.16 (DIR), J5.3
DIR1: A2.16 (DIR), J6.3
ENA0: A1.9 (~EN), J5.2
ENA1: A2.9 (~EN), J6.2
GND: A1.1 (GND), A2.1 (GND), J3.2, J5.1, J6.1
GNDA: A1.7 (GND), A2.7 (GND), J1.2
M00: A1.10 (M0), SW1.8
M01: A1.11 (M1), SW1.7
M02: A1.12 (M2), SW1.6
M10: A2.10 (M0), SW2.8
M11: A2.11 (M1), SW2.7
M12: A2.12 (M2), SW2.6
unnamed: A1.13 (~RST), A1.14 (~SLP), R1.2
unnamed: A2.13 (~RST), A2.14 (~SLP), R2.2
PUL0: A1.15 (STEP), J5.4
PUL1: A2.15 (STEP), J6.4

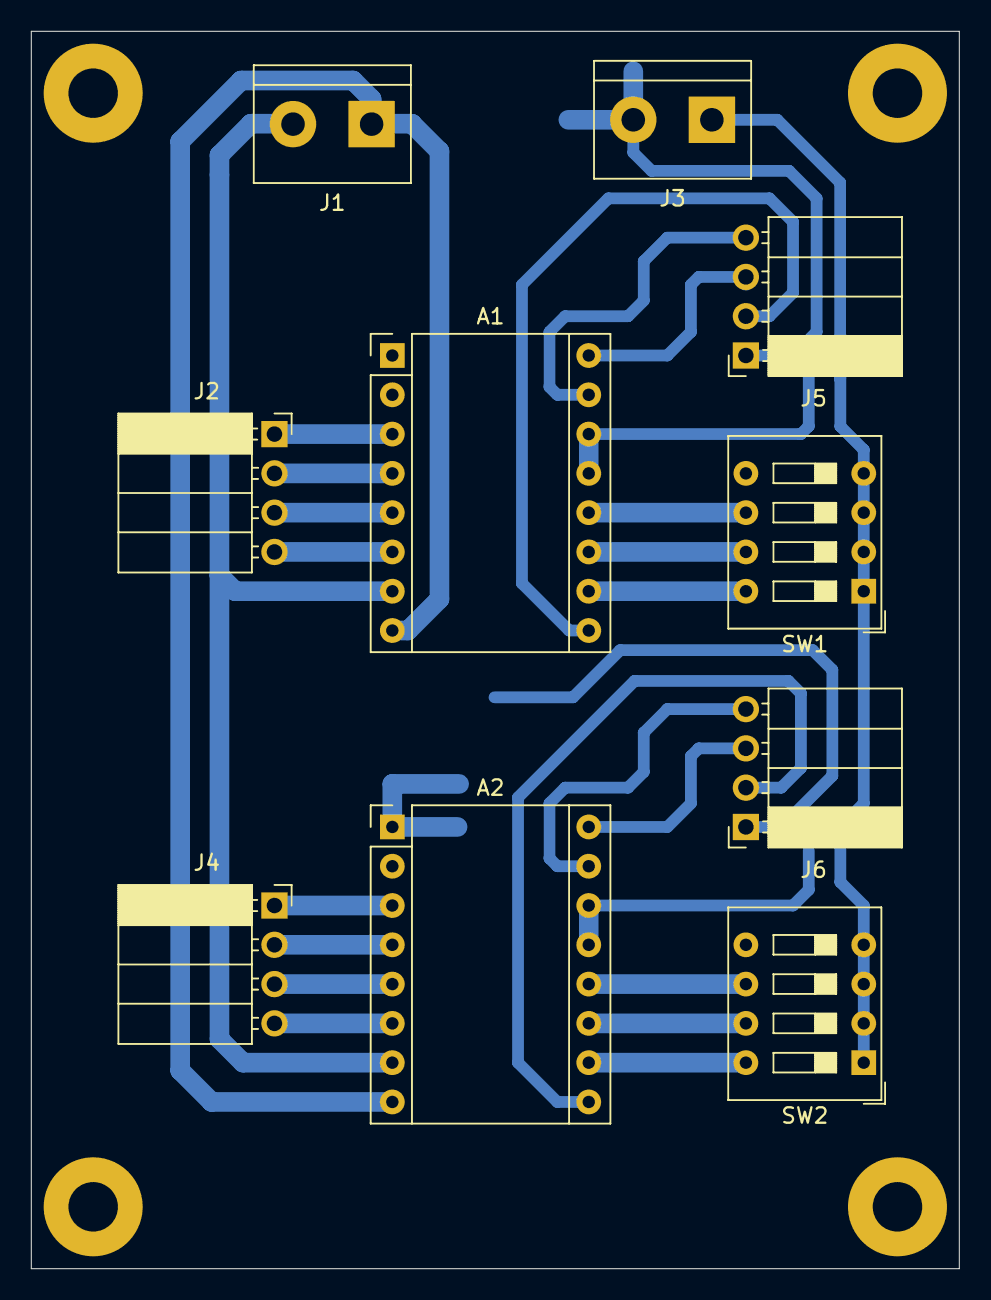
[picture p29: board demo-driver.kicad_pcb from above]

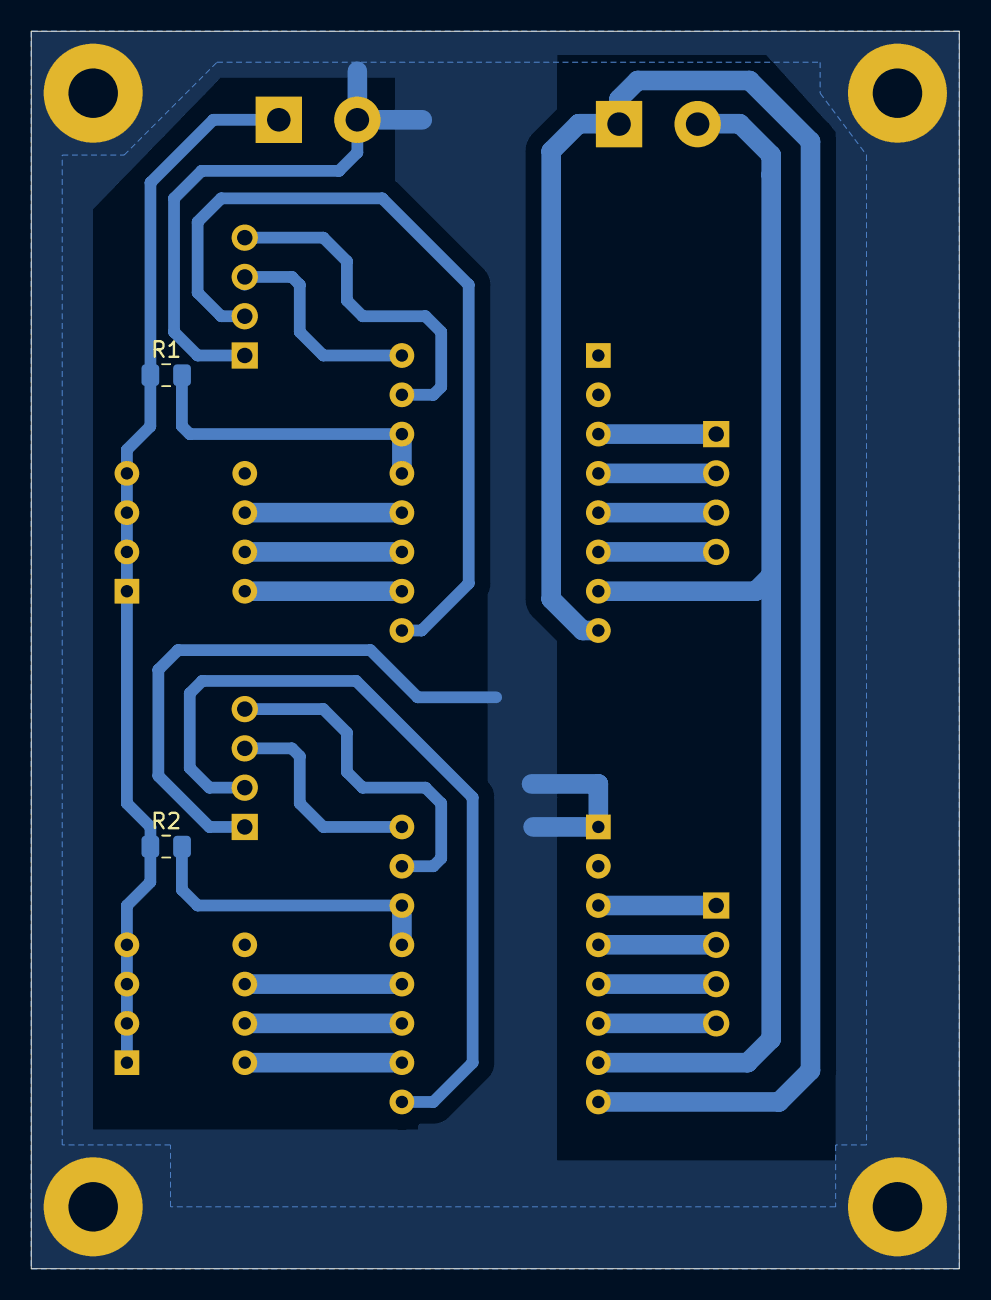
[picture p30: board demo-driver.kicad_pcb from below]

Board: 2 copper layers, 60.0 x 80.0 mm, 12 parts (2 on the bottom side), 26 nets.

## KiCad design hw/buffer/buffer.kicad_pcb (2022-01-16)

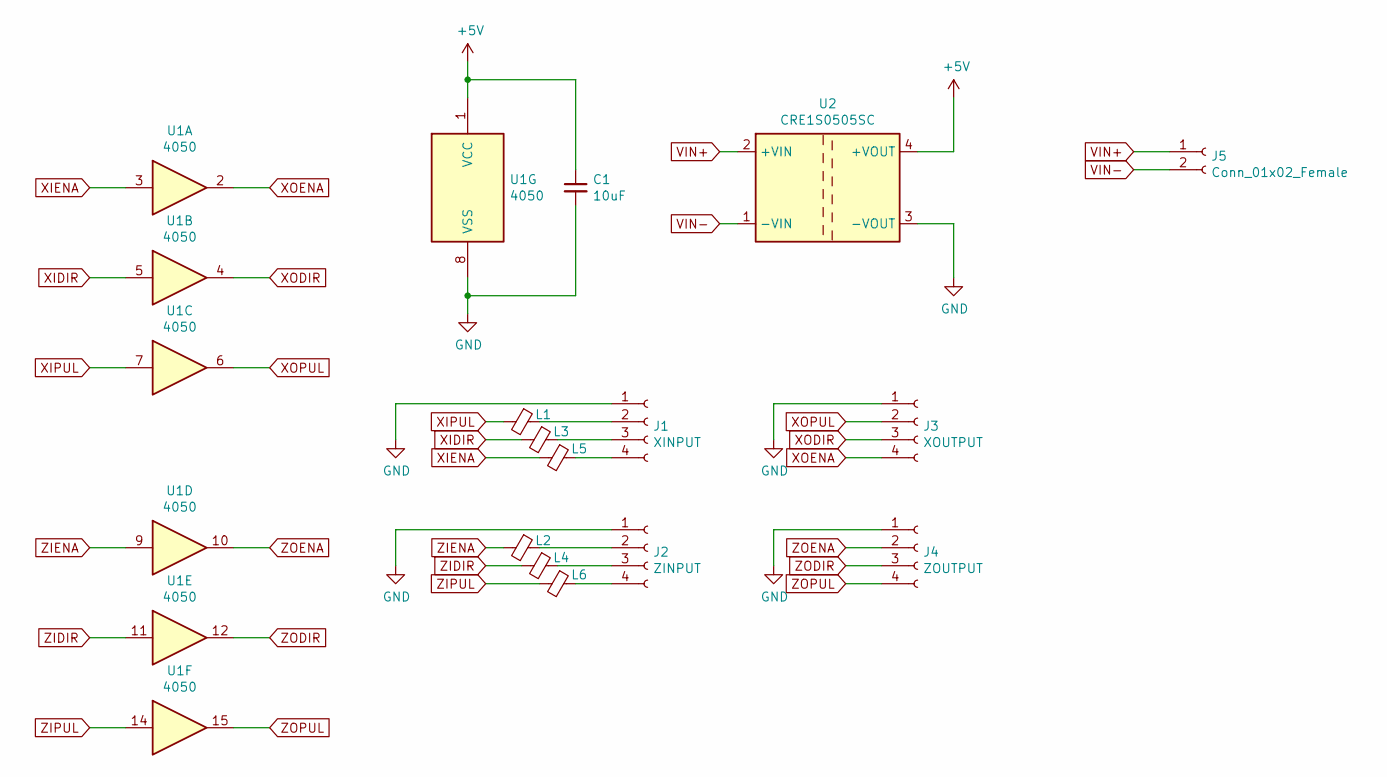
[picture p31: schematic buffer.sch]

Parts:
C1: 10uF; C_0805_2012Metric_Pad1.15x1.40mm_HandSolder
J1: XINPUT; TerminalBlock_bornier-4_P5.08mm
J2: ZINPUT; TerminalBlock_bornier-4_P5.08mm
J3: XOUTPUT; TerminalBlock_bornier-4_P5.08mm
J4: ZOUTPUT; TerminalBlock_bornier-4_P5.08mm
J5: Conn_01x02_Female; TerminalBlock_bornier-2_P5.08mm
L1, L2, L3, L4, L5, L6: Ferrite_Bead_Small; L_0805_2012Metric_Pad1.15x1.40mm_HandSolder
U1: 4050; DIP-16_W7.62mm_Socket_LongPads
U2: CRE1S0505SC; Converter_DCDC_muRata_CRE1xxxxxxSC_THT

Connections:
+5V: C1.1, U1.1 (VCC), U2.4 (+VOUT)
GND: C1.2, J1.1, J2.1, J3.1, J4.1, U1.8 (VSS), U2.3 (-VOUT)
unnamed: J1.2, L1.1
unnamed: J1.3, L3.1
unnamed: J1.4, L5.1
unnamed: J2.2, L2.1
unnamed: J2.3, L4.1
unnamed: J2.4, L6.1
VIN+: J5.1, U2.2 (+VIN)
VIN-: J5.2, U2.1 (-VIN)
XIDIR: L3.2, U1.5
XIENA: L5.2, U1.3
XIPUL: L1.2, U1.7
XODIR: J3.3, U1.4
XOENA: J3.4, U1.2
XOPUL: J3.2, U1.6
ZIDIR: L4.2, U1.11
ZIENA: L2.2, U1.9
ZIPUL: L6.2, U1.14
ZODIR: J4.3, U1.12
ZOENA: J4.2, U1.10
ZOPUL: J4.4, U1.15

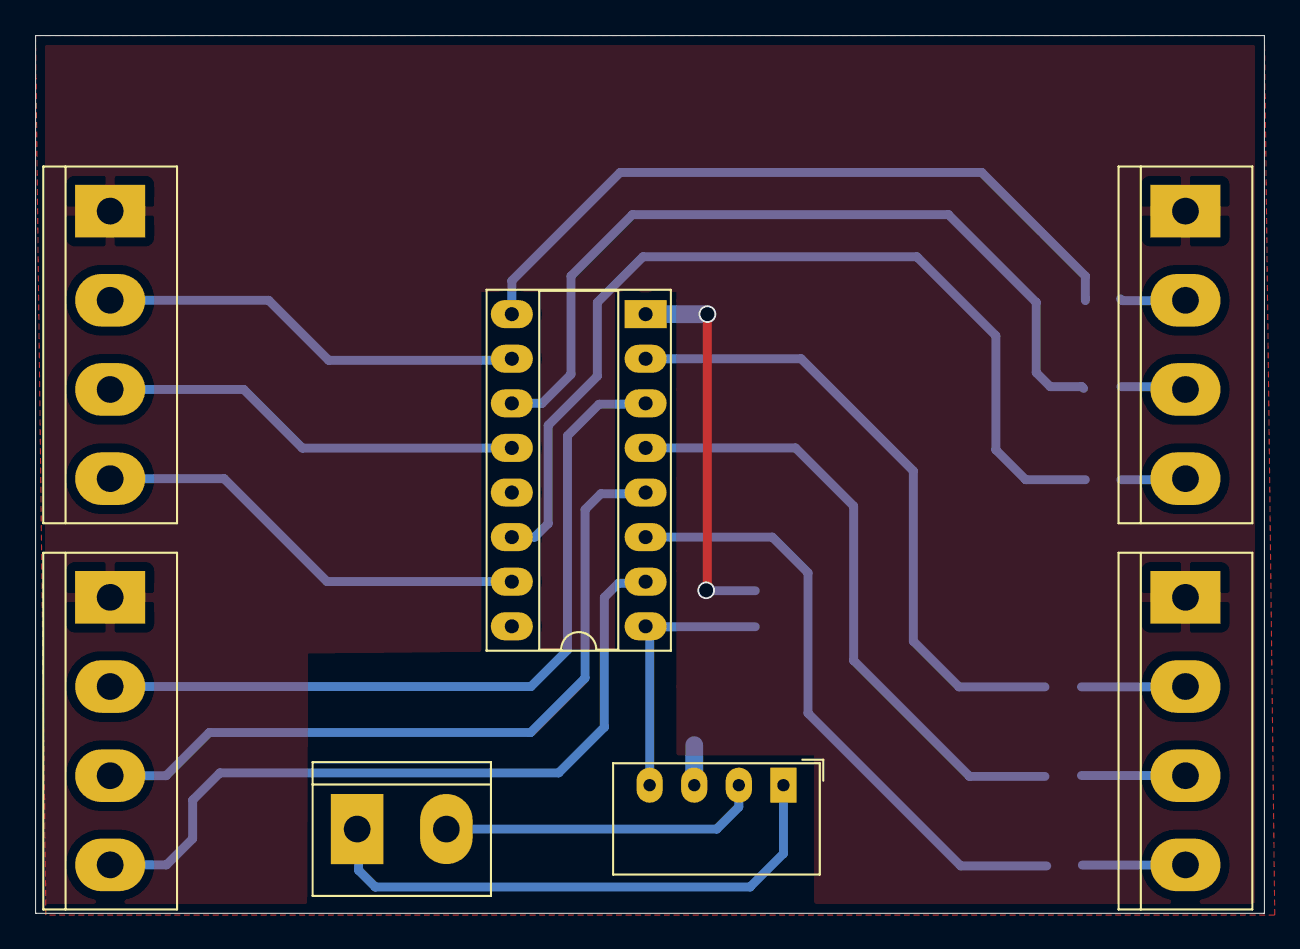
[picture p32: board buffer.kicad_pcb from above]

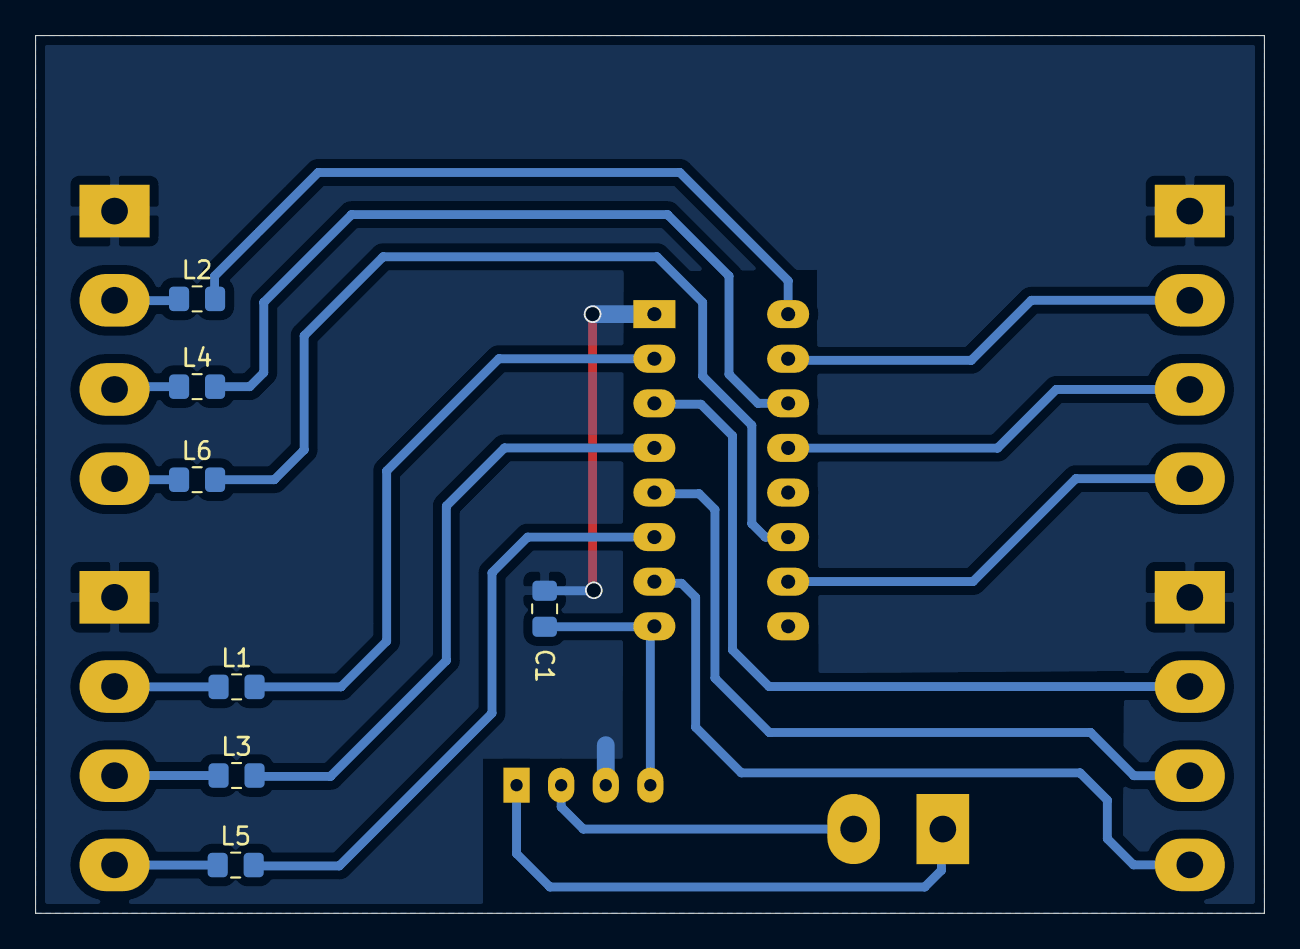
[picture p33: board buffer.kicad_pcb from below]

Board: 2 copper layers, 70.0 x 50.0 mm, 14 parts (7 on the bottom side), 22 nets.

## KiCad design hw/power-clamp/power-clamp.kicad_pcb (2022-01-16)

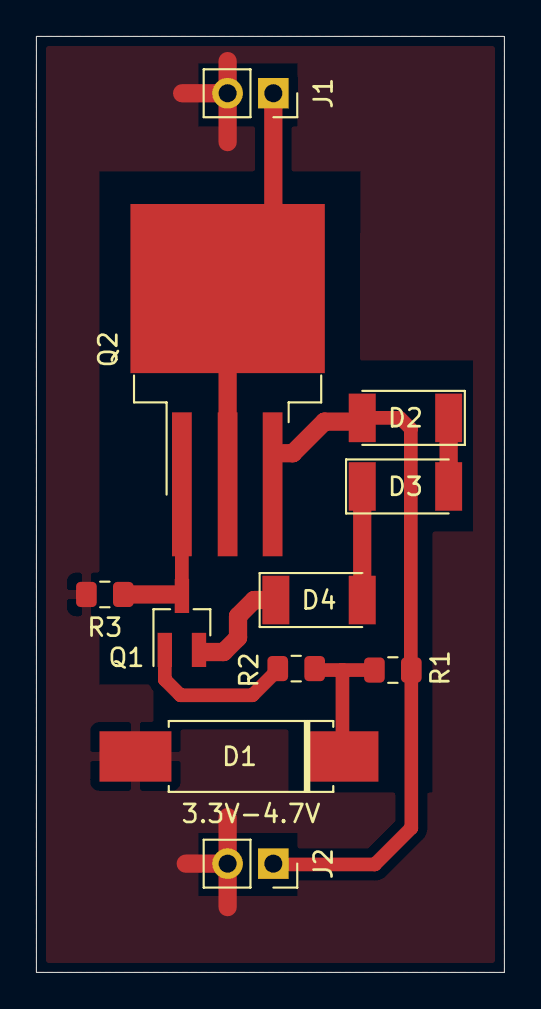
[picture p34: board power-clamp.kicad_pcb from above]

Board: 2 copper layers, 26.0 x 52.0 mm, 11 parts (0 on the bottom side), 9 nets.

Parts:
D1: 3.3V or 4.7V; D_5W_P10.16mm_Horizontal
D2, D3, D4: D_Small_ALT; D_MELF
J1: OUT; PinSocket_1x02_P2.54mm_Vertical
J2: IN; PinSocket_1x02_P2.54mm_Vertical
Q1: Q_PNP_BEC; SOT-23_Handsoldering
Q2: Q_PMOS_GDS; TO-263-3_TabPin2
R1: 1K; R_0805_2012Metric_Pad1.15x1.40mm_HandSolder
R2, R3: 10K; R_0805_2012Metric_Pad1.15x1.40mm_HandSolder

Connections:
+5V: J1.1, Q2.2
GNDA: D1.2, J1.2, J2.2, R3.2
unnamed: D1.1, R1.2, R2.2
unnamed: D2.1, D3.2
unnamed: D3.1, D4.2
unnamed: D4.1, Q1.2
unnamed: Q1.1, R2.1
unnamed: Q1.3, Q2.1, R3.1
VCC: D2.2, J2.1, Q2.3, R1.1

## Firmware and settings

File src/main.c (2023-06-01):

#include <errno.h>
#include <math.h>
#include <stdio.h>
#include <stdlib.h>

#include <libopencm3/cm3/dwt.h>
#include <libopencm3/cm3/nvic.h>
#include <libopencm3/stm32/rcc.h>
#include <libopencm3/stm32/flash.h>
#include <libopencm3/stm32/spi.h>
#include <libopencm3/stm32/gpio.h>
#include <libopencm3/stm32/usart.h>
#include <libopencm3/stm32/exti.h>

//==============================================================================
// Platform
//==============================================================================
#include "clock.h"
#include "delay.h"
#include "gpio.h"
#include "nvic.h"
#include "usart.h"
#include "timer.h"

//==============================================================================
// TFT
//==============================================================================
#include "tft/tft.h"

tft_device_t tft = {
  .ili948x.rd   = {.port = GPIOB, .pin = GPIO0},
  .ili948x.wr   = {.port = GPIOB, .pin = GPIO6},
  .ili948x.rs   = {.port = GPIOB, .pin = GPIO7},
  .ili948x.cs   = {.port = GPIOB, .pin = GPIO8},
  .ili948x.rst  = {.port = GPIOB, .pin = GPIO9},
  .ili948x.data = {.port = GPIOA, .pin = GPIO0 | GPIO1 | GPIO2 | GPIO3 | GPIO4 | GPIO5 | GPIO6 | GPIO7 }
};

//==============================================================================
// ELS Core
//==============================================================================
#include "constants.h"

// peripherals
#include "dro.h"
#include "eeprom.h"
#include "encoder.h"
#include "keypad.h"
#include "spindle.h"
#include "stepper.h"

// config & db
#include "config.h"
#include "kv.h"

// operations
#include "turning.h"
#include "threading.h"

// els functions
#include "function.h"

//==============================================================================
// Helpers
//==============================================================================
static void els_screenshot(void) {
  for (size_t row = 0; row < 320; row++) {
    for (size_t col = 0; col < 480; col++) {
      tft_rgb_t color;
      tft_pixel_get(&tft, col, row, &color);
      printf("%02x%02x%02x", color.r, color.g, color.b);
      if ((col + 1) % 20 == 0)
        printf("\n");
    }
  }
}

//==============================================================================
// Main loop
//==============================================================================
int main(void) {
  els_nvic_setup();
  els_clock_setup();
  els_gpio_setup();
  els_usart_setup();

  printf("\nels v0.1.0 - build %s\n", GIT_SHA);

  // core
  els_timer_setup();

  // peripherals
  els_encoder_setup();
  els_encoder_start();
  els_keypad_setup();

  // IMPORTANT: needs to happen as late as possible.
  els_delay_setup();

  // init kv db & load config
  els_eeprom_setup();
  els_kv_setup();
  els_config_setup();

  els_dro_setup();
  els_stepper_setup();
  els_spindle_setup();

  // setup display
  tft_init(&tft);
  tft_invert(&tft, true);
  //tft_rotate(&tft, ROTATE_90);
  tft_rotate(&tft, ROTATE_270);

  // functions manager, needs to be called after config read.
  els_function_init();

  while (1) {
    switch (els_keypad_peek()) {
      case 0x00:
        els_screenshot();
        els_keypad_flush();
        break;
      case ELS_KEY_LOCK:
        if (els_keypad_locked()) {
          printf("keypad: unlock\n");
          els_keypad_unlock();
        }
        else {
          printf("keypad: lock\n");
          els_keypad_lock();
        }
        els_keypad_flush();
        break;
      case ELS_KEY_ENC_MULT:
        els_encoder_inc_multiplier();
        els_keypad_flush();
        break;
      default:
        if (els_keypad_locked())
          els_keypad_flush();
        break;
    }

    els_function_update();
    els_spindle_update();
  }

  return 0;
}

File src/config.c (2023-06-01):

#include <stdio.h>
#include <stdlib.h>
#include <stdint.h>
#include <string.h>
#include <stdbool.h>
#include <stddef.h>
#include <sys/types.h>

#include "config.h"
#include "encoder.h"
#include "function.h"
#include "keypad.h"
#include "kv.h"
#include "stepper.h"

#include "constants.h"

#include "tft/tft.h"
#include "tft/fonts/fonts.h"

//==============================================================================
// Externs
//==============================================================================
extern tft_device_t tft;

extern const tft_font_t noto_sans_mono_bold_26;
extern const tft_font_t noto_sans_mono_bold_20;
extern const tft_font_t gears_regular_32;
extern const tft_font_t gears_regular_50;

//==============================================================================
// State
//==============================================================================
static els_config_t _els_config;
const els_config_t *els_config = &_els_config;

//==============================================================================
// Internal State
//==============================================================================
typedef enum {
  ELS_CONFIG_X_PULSES_PER_MM      = 0,
  ELS_CONFIG_Z_PULSES_PER_MM      = 1,
  ELS_CONFIG_X_BACKLASH_UM        = 2,
  ELS_CONFIG_Z_BACKLASH_UM        = 3,
  ELS_CONFIG_SPINDLE_ENCODER_PPR  = 4,
  ELS_CONFIG_X_JOG_MM_S           = 5,
  ELS_CONFIG_Z_JOG_MM_S           = 6,
  ELS_CONFIG_X_RETRACT_JOG_MM_S   = 7,
  ELS_CONFIG_Z_RETRACT_JOG_MM_S   = 8,
  ELS_CONFIG_X_CLOSED_LOOP        = 9,
  ELS_CONFIG_Z_CLOSED_LOOP        = 10,
  ELS_CONFIG_X_DRO_INVERT         = 11,
  ELS_CONFIG_Z_DRO_INVERT         = 12,
  ELS_CONFIG_X_DIR_INVERT         = 13,
  ELS_CONFIG_Z_DIR_INVERT         = 14,
} els_config_setting_t;

static struct {
  bool locked;
  int32_t encoder_curr;
  int16_t encoder_multiplier;
  els_config_setting_t setting;
  bool edit;
  uint32_t value;
} config = {
  .encoder_multiplier = 1
};

const char *settings[] = {
  "X PULSES PER MM",
  "Z PULSES PER MM",
  "X BACKLASH uM",
  "Z BACKLASH uM",
  "SPINDLE ENCODER PPR",
  "X JOG MM/S",
  "Z JOG MM/S",
  "X RETRACT JOG MM/S",
  "Z RETRACT JOG MM/S",
  "X CLOSED LOOP",
  "Z CLOSED LOOP",
  "X DRO INVERT",
  "Z DRO INVERT",
  "X DIR INVERT",
  "Z DIR INVERT",
};

#define ELS_CONFIG_SETTING_MAX (sizeof(settings) / sizeof(settings[0]))

//==============================================================================
// Helpers
//==============================================================================

static void     els_config_menu_display_init(void);
static void     els_config_menu_display_header(void);
static void     els_config_menu_display_refresh(void);
static uint32_t els_config_get(size_t n);
static void     els_config_set(size_t n, uint32_t value);
static void     els_config_display_encoder_pips(void);

//==============================================================================
// API
//==============================================================================
void els_config_setup(void) {
  memset(&_els_config, 0, sizeof(_els_config));

  els_kv_read(ELS_KV_X_PULSES_PER_MM, &_els_config.x_pulses_per_mm, sizeof(_els_config.x_pulses_per_mm));
  if (_els_config.x_pulses_per_mm == 0) {
    _els_config.x_pulses_per_mm = ELS_X_PULSES_PER_MM;
    printf("set default x pulses per mm = %lu\n", _els_config.x_pulses_per_mm);
    els_kv_write(ELS_KV_X_PULSES_PER_MM, &_els_config.x_pulses_per_mm, sizeof(_els_config.x_pulses_per_mm));
  }

  els_kv_read(ELS_KV_Z_PULSES_PER_MM, &_els_config.z_pulses_per_mm, sizeof(_els_config.z_pulses_per_mm));
  if (_els_config.z_pulses_per_mm == 0) {
    _els_config.z_pulses_per_mm = ELS_Z_PULSES_PER_MM;
    printf("set default z pulses per mm = %lu\n", _els_config.z_pulses_per_mm);
    els_kv_write(ELS_KV_Z_PULSES_PER_MM, &_els_config.z_pulses_per_mm, sizeof(_els_config.z_pulses_per_mm));
  }

  els_kv_read(ELS_KV_X_BACKLASH_UM, &_els_config.x_backlash_um, sizeof(_els_config.x_backlash_um));
  if (_els_config.x_backlash_um == 0) {
    _els_config.x_backlash_um = ELS_X_BACKLASH_UM;
    printf("set default x backlash um = %lu\n", _els_config.x_backlash_um);
    els_kv_write(ELS_KV_X_BACKLASH_UM, &_els_config.x_backlash_um, sizeof(_els_config.x_backlash_um));
  }
  _els_config.x_backlash_pulses = (_els_config.x_backlash_um * _els_config.x_pulses_per_mm) / 1000;

  els_kv_read(ELS_KV_Z_BACKLASH_UM, &_els_config.z_backlash_um, sizeof(_els_config.z_backlash_um));
  if (_els_config.z_backlash_um == 0) {
    _els_config.z_backlash_um = ELS_Z_BACKLASH_UM;
    printf("set default z backlash um = %lu\n", _els_config.z_backlash_um);
    els_kv_write(ELS_KV_Z_BACKLASH_UM, &_els_config.z_backlash_um, sizeof(_els_config.z_backlash_um));
  }
  _els_config.z_backlash_pulses = (_els_config.z_backlash_um * _els_config.z_pulses_per_mm) / 1000;
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

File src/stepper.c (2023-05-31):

#include <stdio.h>
#include <stdlib.h>
#include <stdint.h>
#include <string.h>
#include <stdbool.h>
#include <stddef.h>
#include <sys/types.h>

#include <libopencm3/cm3/dwt.h>
#include <libopencm3/cm3/nvic.h>
#include <libopencm3/stm32/rcc.h>
#include <libopencm3/stm32/flash.h>
#include <libopencm3/stm32/spi.h>
#include <libopencm3/stm32/gpio.h>
#include <libopencm3/stm32/usart.h>
#include <libopencm3/stm32/exti.h>
#include <libopencm3/stm32/f4/timer.h>

#include "delay.h"
#include "gpio.h"
#include "nvic.h"
#include "timer.h"

#include "stepper.h"

#include "config.h"
#include "constants.h"
#include "dro.h"
#include "utils.h"

#define ELS_TIMER                     TIM7
#define ELS_TIMER_IRQ                 NVIC_TIM7_IRQ
#define ELS_TIMER_RCC                 RCC_TIM7
#define ELS_TIMER_RST                 RST_TIM7

// at 100khz, 100 pulses per second.
#define ELS_TIMER_RELOAD_MAX          500

#define ELS_TIMER_DECEL_STEPS         200

#define ELS_TIMER_ACCEL_X             2
#define ELS_TIMER_DECEL_X             2

#define ELS_TIMER_ACCEL_Z             3
#define ELS_TIMER_DECEL_Z             4

#define DEBUG_POSITION_LOG            0
#define DEBUG_POSITION_LOG_X          0
#define DEBUG_POSITION_LOG_Z          0
#define DEBUG_POSITION_LOG_XZ         0

//==============================================================================
// Internal State
//==============================================================================

#if DEBUG_POSITION_LOG
static double _tsx[40], _tsz[40], _tdx[40], _tdz[40];
static size_t _tidx = 0, _tn = 0;
#endif

typedef enum {
  STEPPER_OP_NA,
  STEPPER_OP_LINE_X,
  STEPPER_OP_LINE_Z,
  STEPPER_OP_LINE_XZ,
  STEPPER_OP_LINE_ZX,
  STEPPER_OP_ARC_Q2_CW,
  STEPPER_OP_ARC_Q3_CCW,
  STEPPER_OP_ARC_Q4_CCW
} stepper_op_t;

static struct {
  els_stepper_t pos;

  int32_t xtarget;
  int32_t ztarget;

  bool z_accel;
  bool x_accel;

  volatile int32_t xsteps;
  double xdelta;
  uint32_t xfeed_um;
  stepper_op_t xop;

  // linear xz movement
  int32_t xz_line_n;
  int32_t xz_line_d;
  int32_t xz_line_err;

  volatile int32_t zsteps;
  double zdelta;
  uint32_t zfeed_um;
  stepper_op_t zop;

  volatile uint32_t xticks, zticks;

  // linear zx movement
  int32_t zx_line_n;
  int32_t zx_line_d;
  int32_t zx_line_err;

  // cw arc movement
  double cw_circle_radius;
  double cw_circle_center_z;
  double cw_circle_center_x;
  double cw_circle_zpos;

  // ccw arc movement
  double ccw_circle_radius;
  double ccw_circle_center_z;
  double ccw_circle_center_x;
  double ccw_circle_zpos;

  uint32_t xreload_target;
  uint32_t zreload_target;

  bool x_enabled;
  bool z_enabled;
} stepper = {
  .x_enabled = false,
  .z_enabled = false,
  .xticks = 0,
  .zticks = 0
};

//==============================================================================
// Exported constant
//==============================================================================
els_stepper_t *els_stepper = &stepper.pos;

//==============================================================================
// Internal functions
//==============================================================================
static void els_stepper_configure_gpio(void);
static void els_stepper_configure_timer(void);
static void els_stepper_configure_axes(void);

static void els_stepper_timer_start(void);
static void els_stepper_timer_stop(void);

static void els_stepper_timer_isr(void) __attribute__ ((interrupt ("IRQ")));
static void els_stepper_timer_x_update(uint32_t feed_um, bool accel);
static void els_stepper_timer_z_update(uint32_t feed_um, bool accel);

static void els_stepper_move_x_accel(double mm, double speed_mm_s, bool accel);
static void els_stepper_move_z_accel(double mm, double speed_mm_s, bool accel);

//==============================================================================
// API
//==============================================================================
void els_stepper_setup(void) {
  els_stepper_configure_axes();
}

void els_stepper_start(void) {
  // gpio & timer
  els_stepper_configure_gpio();
  els_stepper_configure_timer();

  // reset isr
  els_nvic_irq_set_handler(ELS_TIMER_IRQ, els_stepper_timer_isr);

  els_stepper_enable();

  // default
  timer_set_period(ELS_TIMER, ELS_TIMER_RELOAD_MAX);

  stepper.xtarget = (int32_t)round((stepper.pos.xpos * 1e3));
  stepper.ztarget = (int32_t)round((stepper.pos.zpos * 1e3));

  els_stepper_timer_start();
}

void els_stepper_stop(void) {
  els_stepper_timer_stop();
  els_stepper_disable();
}

void els_stepper_sync(void) {
  if (els_config->x_closed_loop)
    stepper.pos.xpos = els_dro.xpos_um * 1e-3;

  if (els_config->z_closed_loop)
    stepper.pos.zpos = els_dro.zpos_um * 1e-3;
}

void els_stepper_set_xdir_incr(void) {
  if (els_config->x_dir_invert)
    els_gpio_set(ELS_X_DIR_PORT, ELS_X_DIR_PIN);
  else
    els_gpio_clear(ELS_X_DIR_PORT, ELS_X_DIR_PIN);
}

void els_stepper_set_xdir_decr(void) {
  if (els_config->x_dir_invert)
    els_gpio_clear(ELS_X_DIR_PORT, ELS_X_DIR_PIN);
  else
    els_gpio_set(ELS_X_DIR_PORT, ELS_X_DIR_PIN);
}

void els_stepper_set_zdir_incr(void) {
  if (els_config->z_dir_invert)
    els_gpio_clear(ELS_Z_DIR_PORT, ELS_Z_DIR_PIN);
  else
    els_gpio_set(ELS_Z_DIR_PORT, ELS_Z_DIR_PIN);
}

void els_stepper_set_zdir_decr(void) {
  if (els_config->z_dir_invert)
    els_gpio_set(ELS_Z_DIR_PORT, ELS_Z_DIR_PIN);
  else
    els_gpio_clear(ELS_Z_DIR_PORT, ELS_Z_DIR_PIN);
}

void els_stepper_move_x(double mm, double speed_mm_s) {
  els_stepper_move_x_accel(mm, speed_mm_s, true);
}

void els_stepper_move_x_no_accel(double mm, double speed_mm_s) {
  els_stepper_move_x_accel(mm, speed_mm_s, false);
}
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

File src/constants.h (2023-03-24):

#pragma once

#ifdef __cplusplus
extern "C" {
#endif

//=============================================================================
// Indicator LED
//=============================================================================
#define LED_PORT GPIOC
#define LED_PIN  GPIO9

//=============================================================================
// Defaults
//=============================================================================
#define ELS_Z_PULSES_PER_MM   (400)
#define ELS_X_PULSES_PER_MM   (400)

#define ELS_Z_BACKLASH_UM     (120)
#define ELS_X_BACKLASH_UM     (225)

// backlash pulse period / 2
#define ELS_BACKLASH_DELAY_US (1e3)

#define ELS_Z_MAX_MM          (550)
#define ELS_X_MAX_MM          (150)

// Actual PPR of the spindle encoder, factoring in any gear ratio.
#define ELS_S_ENCODER_PPR     (1200)
//=============================================================================
// Z-Axis Pins
//=============================================================================
#define ELS_Z_ENA_PORT        GPIOB
#define ELS_Z_ENA_PIN         GPIO13
#define ELS_Z_DIR_PORT        GPIOB
#define ELS_Z_DIR_PIN         GPIO14
#define ELS_Z_PUL_PORT        GPIOB
#define ELS_Z_PUL_PIN         GPIO15
#define ELS_Z_ENA_ACTIVE_LOW  1

//=============================================================================
// X-Axis Pins
//=============================================================================
#define ELS_X_ENA_PORT        GPIOC
#define ELS_X_ENA_PIN         GPIO13
#define ELS_X_DIR_PORT        GPIOC
#define ELS_X_DIR_PIN         GPIO14
#define ELS_X_PUL_PORT        GPIOC
#define ELS_X_PUL_PIN         GPIO15
#define ELS_X_ENA_ACTIVE_LOW  1

//=============================================================================
// Spindle Encoder
//=============================================================================

// ----------------------------------------------------------------------------
// Settings for spindle module that uses timer in encoder mode.
//
// IMPORTANT: These pins are tied to timer config in spindle.c and should not
//            be updated in isolation.
// ----------------------------------------------------------------------------
// Timer in encoder mode counts on rise & fall.
//
#define ELS_S_ENCODER1_PPR    (ELS_S_ENCODER_PPR * 2)
#define ELS_S_ENCODER1_PORTA  GPIOC
#define ELS_S_ENCODER1_PINA   GPIO6
#define ELS_S_ENCODER1_AFA    GPIO_AF2

#define ELS_S_ENCODER1_PORTB  GPIOC
#define ELS_S_ENCODER1_PINB   GPIO7
#define ELS_S_ENCODER1_AFB    GPIO_AF2

// ----------------------------------------------------------------------------
// Settings for threading module that uses interrupts to keep track of spindle.
// ----------------------------------------------------------------------------
// Interrupt counts on rise
//
#define ELS_S_ENCODER2_PPR    (ELS_S_ENCODER_PPR)
#define ELS_S_ENCODER2_PORTA  GPIOB
#define ELS_S_ENCODER2_PINA   GPIO3
#define ELS_S_ENCODER2_PORTB  GPIOB
#define ELS_S_ENCODER2_PINB   GPIO4

#define ELS_S_ENCODER2_IRQ    NVIC_EXTI3_IRQ
#define ELS_S_ENCODER2_EXTI   EXTI3

//=============================================================================
// Input Encoder
//=============================================================================
#define ELS_I_ENCODER_PPR     (100)

#define ELS_I_ENCODER_PORTA   GPIOC
#define ELS_I_ENCODER_PINA    GPIO2

#define ELS_I_ENCODER_PORTB   GPIOC
#define ELS_I_ENCODER_PINB    GPIO3

//-----------------------------------------------------------------------------
// These need to be updated based on the config above.
//-----------------------------------------------------------------------------
#define ELS_I_ENCODER_ISR     exti2_isr
#define ELS_I_ENCODER_IRQ     NVIC_EXTI2_IRQ
#define ELS_I_ENCODER_EXTI    EXTI2

//=============================================================================
// PS/2 Keypad D-8203
//=============================================================================
#define ELS_KEYPAD_CLK_PORT   GPIOC
#define ELS_KEYPAD_CLK_PIN    GPIO4
#define ELS_KEYPAD_DAT_PORT   GPIOC
#define ELS_KEYPAD_DAT_PIN    GPIO5

//-----------------------------------------------------------------------------
// These need to be updated based on the config above.
//-----------------------------------------------------------------------------
#define ELS_KEYPAD_ISR        exti4_isr
#define ELS_KEYPAD_IRQ        NVIC_EXTI4_IRQ
#define ELS_KEYPAD_EXTI       EXTI4

//-----------------------------------------------------------------------------
// PS/2 keypad scancodes, update if the keypad changes.
//-----------------------------------------------------------------------------
#define ELS_KEY_EOF           -1
#define ELS_KEY_OK            0x25
#define ELS_KEY_EXIT          0x26
#define ELS_KEY_SET_FEED      0x24
#define ELS_KEY_REV_FEED      0x2b

// basic functions that are manually driven on x-axis
#define ELS_KEY_FUN_TURN      0x34
#define ELS_KEY_FUN_THREAD    0x33
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

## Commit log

2022-01-16 initial commit.
    [buffer-B_Cu.gbr, buffer-B_Mask.gbr, buffer-Dwgs_User.gbr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]
2022-04-16 add cut diamond knurling.
2022-10-12 various bugfixes and improvements.
    [bore_dimension.c, bore_hole.c, concave_ext_r.c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]
2022-10-13 simplify stepper acceleration logic.
2022-10-13 Initial migration of els Kicad files to Kicad 6.0
    [els.kicad_pcb, els.kicad_sch]
2022-10-13 update kicad 3d model paths.
    [els.kicad_pcb]
2022-10-26 increase thread pitch resolution & bug fixes.
    [threading.c, threading_ext.c, threading_int.c]
2022-11-01 simplify trapezoidal velocity profile for jogging.
    simplify trapezoidal velocity profile
    add config option for jog velocity
2023-02-15 some new features, new functions & bugfixes
    added parting, facing
    added roughing & finishing pass config for turning.
    [bore_dimension.c, bore_hole.c, concave_ext_r.c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]
2023-03-18 updated docs & ext threading improvements.
2023-03-24 feature improvements & updates
    - streamline manual turning & threading jog functions
    - simplify keypad functions
    - replaced min/max jog min/jog max with jog to origin
    - add jog to origin across all modules
    - add closed loop support for manual turning and threading
    [bore_dimension.c, bore_hole.c, concave_ext_r.c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]
2023-04-15 Update hand wheel encoder hw description
    There are a few different options for the hand wheel encoder. According to the schematic, this was built with the 4-wire 5v version in mind.
2023-05-21 Update els.md
    Add solder bridge modifications & changes.
2023-06-03 fix ili9488 driver init.
    [ili948x.c]
2023-06-03 update ili9481 vcom & power init.
    vcom amplitude should be < 6v
